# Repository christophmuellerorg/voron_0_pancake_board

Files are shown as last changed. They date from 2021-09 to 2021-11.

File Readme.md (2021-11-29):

# Pancake Board

The pancake board is a passive tool board mounting on the back of the MiniAB pancake 
stepper of the Voron 0.1. The board solidly mounts with 20mm brass standoffs to the 
back of the mini after burner mounting screws and provides JST PH connectors 
(2mm pitch) for the two part cooling fans, the hotend fan, a thermistor, 
two switches (for example the X endstop + a klicky probe) as well as the stepper. 
The heater output is provided as a 2x1 Molex Microfit connector and all terminals 
are terminated onto a 2x7 Microfit.

# BOM

For the PCB:
- 1x Molex 43045-1400 (Microfit 2x7) 
- 1x Molex 43045-0200 (Microfit 2x1)
- 4x JST PH 2 Pin, B2B-PH-K-S(LF)(SN)
- 3x JST PH 3 Pin, B3B-PH-K-S(LF)(SN)
- 1x JST PH 4 Pin, B4B-PH-K-S(LF)(SN)

And the appropriate connectors for your cable loom...

# Where can I get it?

- [deepfriedhero](https://deepfriedhero.in/products/voron-v0-1-pancake-stepper-board)
- [pcbway](https://www.pcbway.com/project/shareproject/Pancake_Board.html) Disclaimer: I get 10% commission as store credits which I use for future prototypes.
- Or use the gerber files to order from your favourite PCB manufacturer...

# What is the pinout?

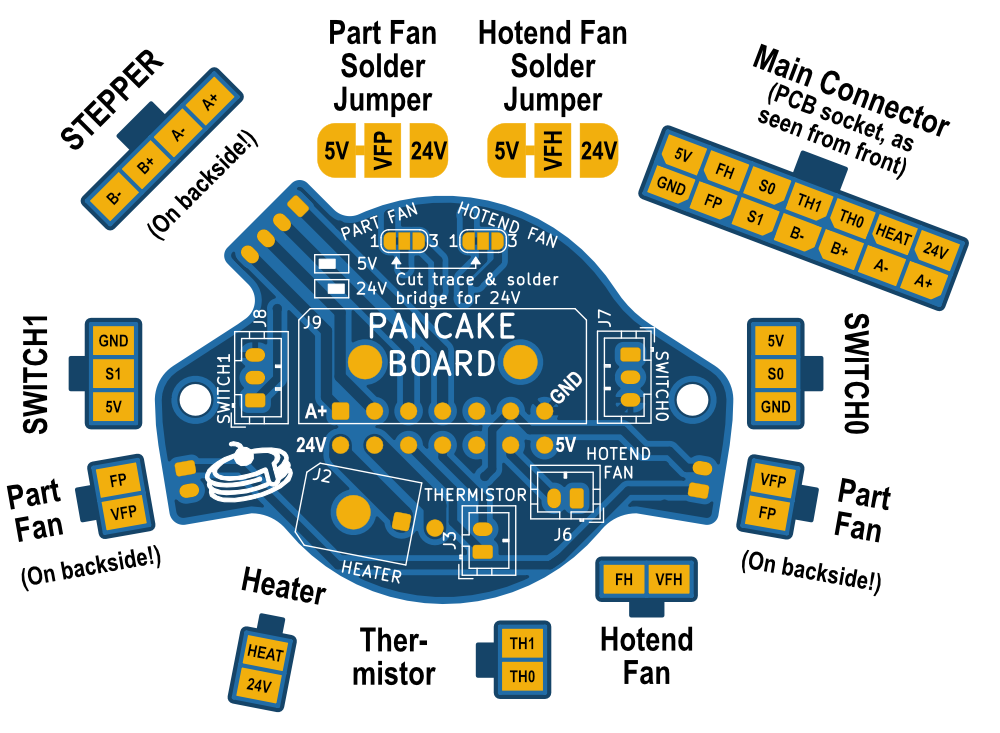
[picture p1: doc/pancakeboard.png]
The pinout...


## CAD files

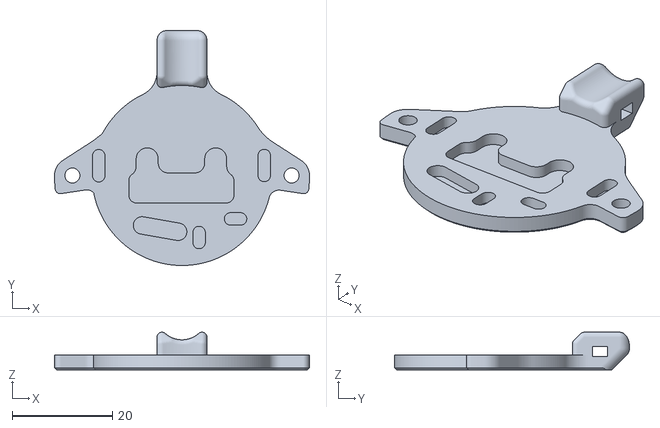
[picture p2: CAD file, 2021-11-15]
stl/backingplate.stl
51.0 x 47.0 x 7.53

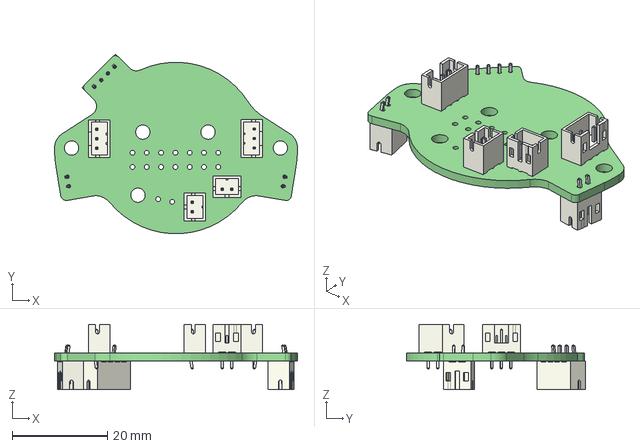
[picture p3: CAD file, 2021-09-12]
v0_miniAB_pancake_board.step
51.0 x 37.6 x 13.7 mm

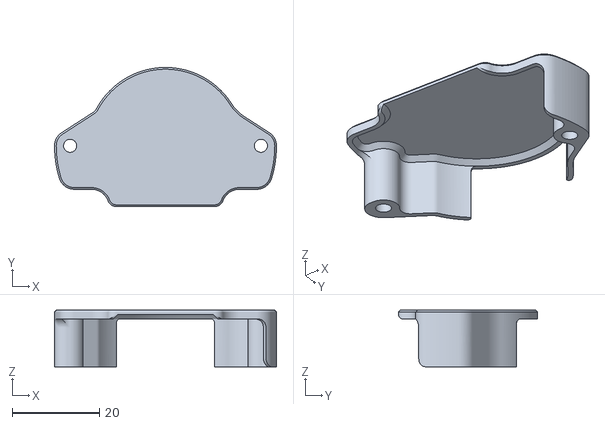
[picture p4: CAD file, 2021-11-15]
stl/cover.stl
51.0 x 32.0 x 13.0

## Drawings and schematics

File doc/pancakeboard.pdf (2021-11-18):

### Part Fan Solder

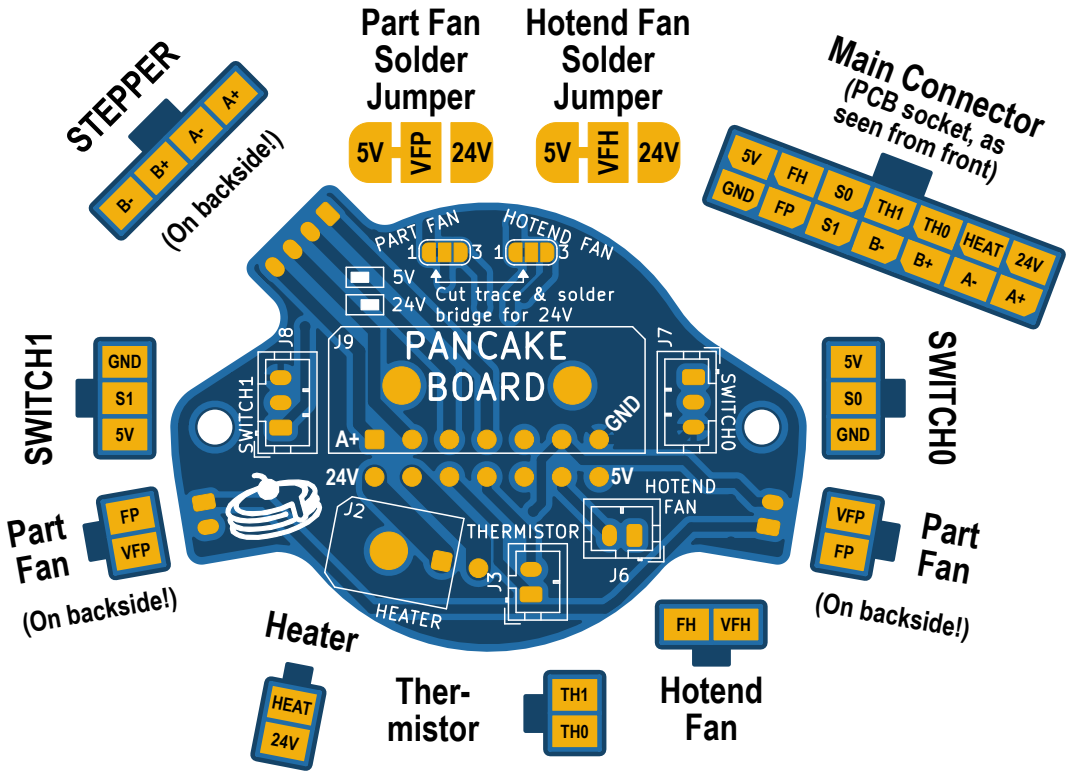
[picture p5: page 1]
GND; 5V FH S0 TH1 TH0 HEAT 24V; GND FP S1 B- B+ A- A+; Main Connector; VFP; STEPPER; HEAT; VFH; Jumper; Hotend Fan Solder Jumper; SWITCH1; Part Fan; Hotend Fan; Ther- mistor; Heater; SWITCH0; (On backside!)

(PCB socket, as

seen from front)

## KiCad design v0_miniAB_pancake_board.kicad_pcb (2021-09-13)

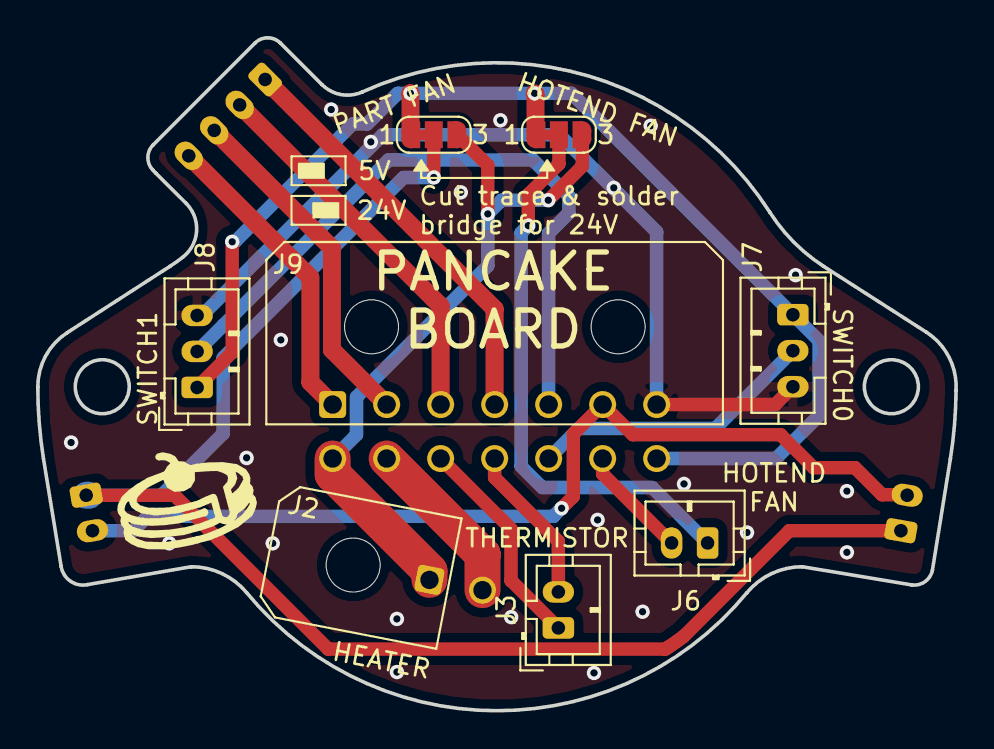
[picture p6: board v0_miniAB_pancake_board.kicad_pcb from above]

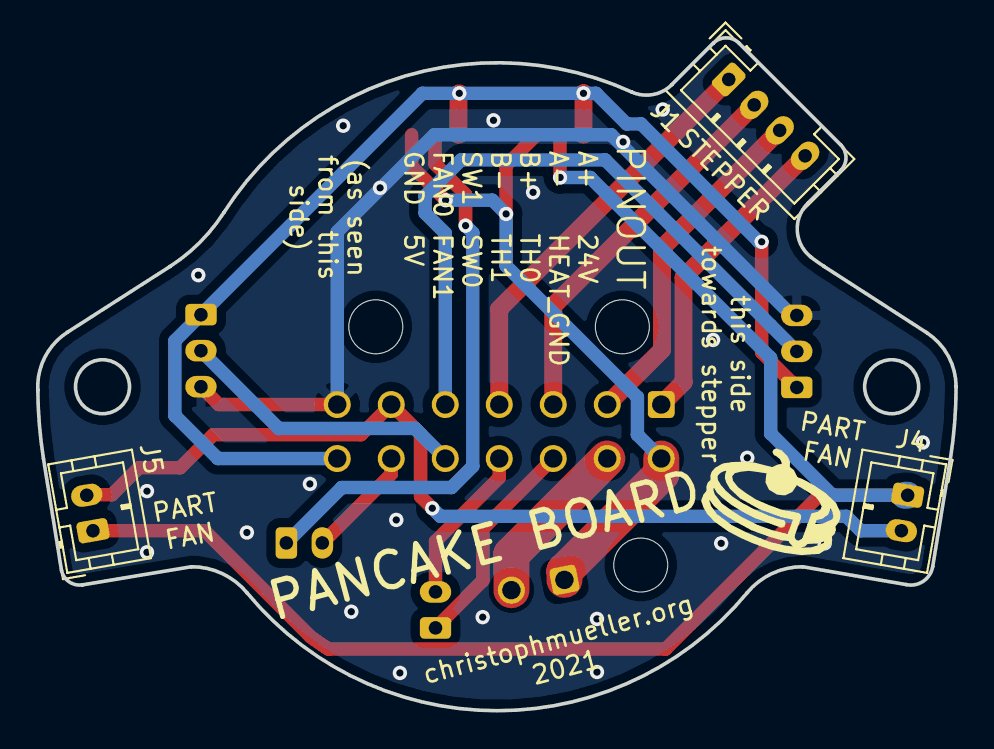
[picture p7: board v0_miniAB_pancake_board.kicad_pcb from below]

Board: 2 copper layers, 51.0 x 37.4 mm, 11 parts (3 on the bottom side), 16 nets.

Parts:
J1: Conn_01x04_Female; JST_PH_B4B-PH-K_1x04_P2.00mm_Vertical
J2: Conn_01x02_Female; Molex_Micro-Fit_3.0_43045-0200_2x01_P3.00mm_Horizontal
J3, J4, J5, J6: Conn_01x02_Female; JST_PH_B2B-PH-K_1x02_P2.00mm_Vertical
J7, J8: Conn_01x03_Female; JST_PH_B3B-PH-K_1x03_P2.00mm_Vertical
J9: Conn_02x07_Counter_Clockwise; Molex_Micro-Fit_3.0_43045-1400_2x07_P3.00mm_Horizontal
J10, J11: Conn_01x03_Female; SolderJumper-3_P1.3mm_Bridged12_RoundedPad1.0x1.5mm_NumberL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

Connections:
+5V: J7.1, J8.1, J9.14, J10.1, J11.1
+24V: J2.1, J9.8, J10.3, J11.3
/A+: J1.4, J9.1
/A-: J1.3, J9.2
/B+: J1.2, J9.3
/B-: J1.1, J9.4
/VFAN0: J4.1, J5.1, J10.2
/VFAN1: J6.1, J11.2
/fan0: J4.2, J5.2, J9.6
/fan1: J6.2, J9.13
/heat_gnd: J2.2, J9.9
/sw0: J7.2, J9.12
/sw1: J8.2, J9.5
/therm0: J3.1, J9.10
/therm1: J3.2, J9.11
GND: J7.3, J8.3, J9.7

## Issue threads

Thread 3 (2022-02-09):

Incorrect Wiring Diagram

aTinyShellScript, 2022-02-09:
Unless I'm really bad at reading wiring diagrams, this one is wrong. I just smoked my parts fans with reverse voltage.

Please excuse my horrible paint skills but the below shows how it should be labeled.

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

christophmuellerorg, 2022-02-10:
Note where the nose of the connector on the backside silkscreen is - the connection should be correct, but the connector rotates over on the backside swapping VFP and FP.

aTinyShellScript, 2022-02-10:
The silkscreen shows it with the centering tab facing out, like it does in the diagram. I don't see a way to read this diagram without wiring it backwards. If it is to match how the stepper connector is shown, then the tabs on the diagram for the part fans should be on the inside, not the outside.

Just want to save other people the headache of replacing fans.

KayosMaker, 2022-02-14:
I also read this backwards when i wired mine up.  fortunately i did all one color wire, and needed to go through and probe to id them, when i caught the reversed wires.  it doesnt read well as illustrated.  it should be drawn as seen from the same side of the board as the rest, or there should perhaps be a second illustration with the other side drawn out as seen.  it would be less confusing.  cool board though i love it!

Turge08, 2022-04-20:
Burning 2 fans due to wrong polarity brought me here . I'm not sure how I could've interpreted it any other way though...

jmeier5261, 2024-06-20:
I smoked my fans because of this when I installed this board a while back, then found this thread and fixed it. Now 8 months later I smoked 2 fans again rebuilding my toolhead because I forgot this was incorrect

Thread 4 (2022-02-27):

Pcb connecter questions

jollywombats, 2022-02-27:
Pardon the question, but is there a matching PCB I am missing for this other than the standard umbilical breakout board?  I ask since that one does not have support for the additional switch the pancake board supports, and obviously the molex wiring would not match up as they are different traces to the pins. Anyone have a suggestion on this one that I am missing. Thank you!

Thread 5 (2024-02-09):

24 Volt wiring

Tmallard, 2024-02-09:
Sorry for the dumb question here (Mechanical guy making sparks). I have my board configured to run a 24v part fan. I am confused on how to wire it to my SKR3 EZ board. Both the heater and the fans share a 24v input. Am I supposed to supply a constant 24v and use a single wire for "Heat" and "FP" assuming the switching of the PWM happens on the GND side?

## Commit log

2021-09-12 beta version \o/
    [v0_miniAB_pancake_board-B_Cu.gbr, v0_miniAB_pancake_board-B_Mask.gbr, v0_miniAB_pancake_board-B_Paste.gbr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]
2021-09-12 step file added
    [v0_miniAB_pancake_board.step]
2021-09-13 a little bit more clearance around the mounting holes
    [v0_miniAB_pancake_board-B_Cu.gbr, v0_miniAB_pancake_board-B_Mask.gbr, v0_miniAB_pancake_board-B_Paste.gbr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]
2021-11-15 STLs added
    [backingplate.stl, cover.stl]
2021-11-29 connector naming fixed
